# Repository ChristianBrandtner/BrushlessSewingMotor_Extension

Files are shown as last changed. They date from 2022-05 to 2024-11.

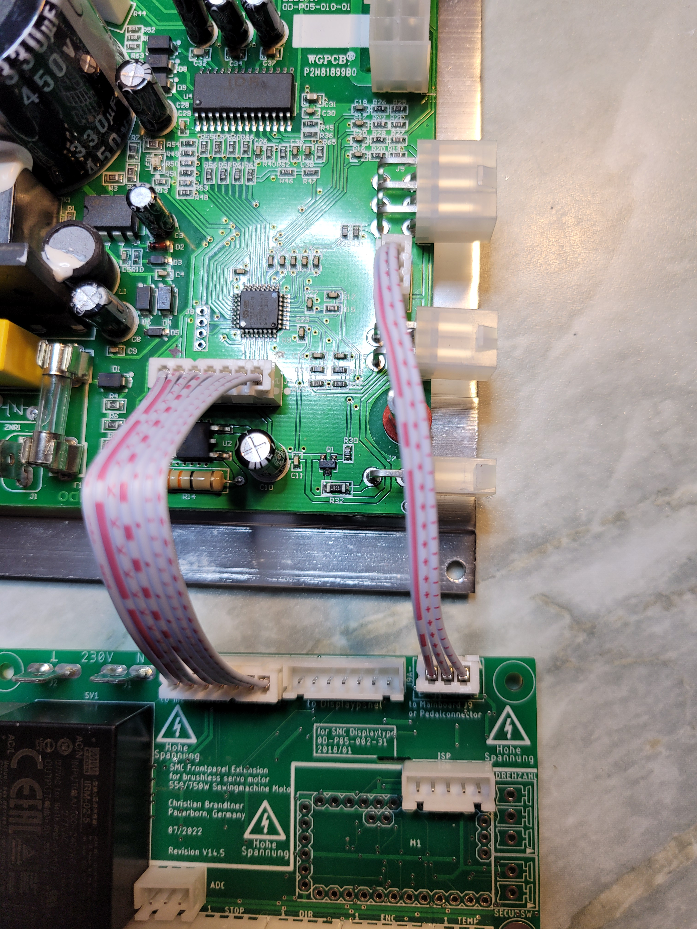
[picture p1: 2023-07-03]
Hardware/WithGalvanicIsolation/Arduino/picture/20221205_171128.jpg

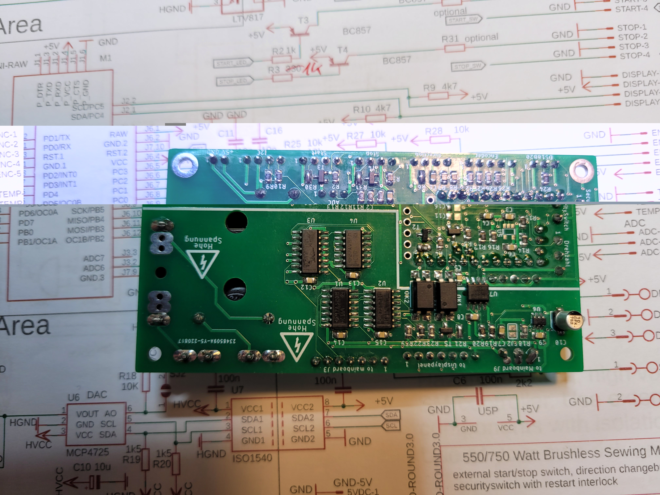
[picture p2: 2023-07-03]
Hardware/WithGalvanicIsolation/Arduino/picture/20221206_175256.jpg

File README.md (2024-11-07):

# BrushlessSewingMotor_Extension
&nbsp;&nbsp;&nbsp;&nbsp;&nbsp;&nbsp;&nbsp;&nbsp;&nbsp;&nbsp;


contact: github1@brandtner.net

## 11/2022  ! Project is in progress, ask before you order PCB or other things. !

## INTRODUCTION

This is a extension for a cheap chinese 550/750W brushless servo motor for external control of speed, direction, etc.
to use in in e.g. Mini Lathe

first test with switch and potentiometer:
https://www.youtube.com/watch?v=qao7Rex1lZU

SMC_Motor

## STATUS
7.11.2024

Ein neues ISO Interface ist in Arbeit aber noch nicht fertiggestellt. 
Die Software ermöglicht es jetzt die komplette Steuerung des Motorkontollers zu übernehmen, inklusive der Einstellungen für die Motorparameter im Kontroller. Das bedeutet daß das Bedienpanel des BLDC-Motors nicht mehr in Griffweite sein muss.

Im Moment pausiert die Entwicklung weil zuwenig Bedarf dafür zu erkennen ist.

A new ISO interface is in the works but not yet finished. The software now makes it possible to take over complete control of the motor controller, including the settings for the motor parameters in the controller. This means that the control panel of the BLDC motor no longer has to be within reach.

Development is currently on hold because there is not enough demand for it.

14.2.2023



RPM Sensor



05.09.2022

Beim Einbau in das Steuergehäuse habe ich nun festgestellt das es Änderungsbedarf gibt, es ist ziemlich eng und die Anordnung der Anschlüsse passt nicht so wirklich gut.
Eingebaut_V1

Deshalb wird es eine zweigeteilte Lösung geben, 1. das Iso Ínterface, montiert auf dem SMC Controller, 2. davon getrennt die Steuerungsplatine, dann neu mit einem Ardunino Nano wegen der USB-Schnittstelle für einfache Updates.
Durch die Trennung ergibt sich auch die Mögichkeit eine andere Steuerung zu verwenden, z.B. Blackpill STM32F411. Der Ardunio ist schon arg an der Grenze des Flashspeichers.
Steuerung_geplant

Next Version (11/2022):

IsoInterface_geplant_v16

08.07.2022

Die ursprüngĺiche Planung auf eine Hardwaredrehzahlmessung zu verzichten werde ich nicht mehr weiterverfolgen.
Die Softwarelösung funktioniert zwar zufriedenstellend, auch unter berücksichtigung des Getriebeschalters und der Untersetzungen von Motor und Getriebe, aber der Atmega ist durch die vielen Einstellungsmenüs am Ende der Kapazität.
Deshalb ist ein Drehzahlsensor an der Spindel erforderlich, damit entfällt die ganze Software für die Drehzahlberechnung und es ist Platz um die Schnittgeschwindigkeit für den Werkstückdurchmesser anzuzeigen.
Das finde ich nützlicher als den Drehzahlsensor einzusparen.
An der Hardware der Platine ändert sich nichts, war alles schon vorgesehen.

07.07.2022

Version 14.5

Änderungen an der Platine
Grund:
Einfügen eines optionalen ISP-Steckers.
Anschluss der RPM Sensors nach PB0 (ICP1) verlegt.
optinonal weitere Anschlussbuchse für den Pedalanschluss vorgesehen, zum direkten Kabelanschluss des Pedalkabels
an den originalen Stecker des SMC. Kein zusätzlicher JST Stecker J9 auf dem SMC Board notwendig. 

22.6.2022

Version 14.2

Änderungen an der Platine
Grund:
JST Stecker J3 Fehler in der Ausrichtung beseitigt

20.6.2022

Version 14.1

Änderungen an der Platine
Grund:
OK2 Anschlüsse vertauscht, optionale Widerstände R6,R30,R31
JST Stecker J3, Ausrichtung getauscht damit fertig konfektionierte Kabel zum SMC verwendet werden können.
Schaltung getestet (ohne RPM-Sensor und analog 0-10V Eingang, alles optional)

Wesentliche Funktionen der Software funktionieren:
Drehzahlregelung, Richtungsumschaltung, Drehzahlanzeige

03.06.2022 New PCB Version 12.2, Errors in PCB layout fixed. Basic software in progress.

12.05.2022 PCB Version 11.5 with galvanic isolation is in production 

30.04.2022 The goal is to fit the SMC controller board and everything else into the existing lathe front casing.

29.04.2022 optoisolation with separate powersupply is in work.

28.04.2022 under construction and brainstorming.

## PREVIEW

Display3
Display4

## TODO

TODO: finalize software

## Features

- no changes on Controlerboard or Panelboard needed; 
- can be installed in the housing on existing attachments; 
- speedcontrol, rotary encoder;
- start/stop control,  button with LED; 
- rotation direction control, button with LED;
- securityswitch input for chuck guard;
- spindel RPM display (calculated and maesured)
- original SMC displaypanel can be used at same time 
- high temperture warning;
- rampup and down at start/stop
- isolated inputs/outputs for galvanic isolation from the mains voltage

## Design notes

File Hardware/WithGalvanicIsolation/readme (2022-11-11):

11.11.2022
Version 14.5 only for testing, not production.

The next version consists of two boards, ISO board and STM32 control board

07.07.2022
Version 14.5
Änderungen an der Platine
Grund:
Einfügen eines optionalen ISP-Steckers.
Anschluss der RPM Sensors nach PB0 (ICP1) verlegt.
optinonal weitere Anschlussbuchse für den Pedalanschluss vorgesehen, zum direkten Kabelanschluss des Pedalkabels
an den originalen Stecker des SMC. Kein zusätzlicher JST Stecker J9 auf dem SMC Board notwendig. 

22.6.2022
Version 14.2
Änderungen an der Platine
Grund:
JST Stecker J3 Fehler in der Ausrichtung beseitigt

20.6.2022
Version 14.1
Änderungen an der Platine
Grund:
OK2 Anschlüsse vertauscht, optionale Widerstände R6,R30,R31
JST Stecker J3, Ausrichtung getauscht damit fertig konfektionierte Kabel zum SMC verwendet werden können.
Schaltung getestet (ohne RPM-Sensor und analog 0-10V Eingang, alles optional)

3.6.2022
Version 12.2
Änderungen an der Platine
Grund:
Fehler im Footprint des Arduino Pro Mini, J3.1 und J3.3 vertauscht
Signal Direction_SW von ADC7(A7) zu PB3(D11) verlegt ( wg. Arduino Kompatibilität)
Autorouter Layout verbessert

31.5.2022
Änderungen an der Platine
Neue Version 12.1
Grund:
SDA/SCL zwischen U6 und U7 vertauscht
C11 entfällt
C8,C5 näher an U7 Pins
R29 hinzu, für Betrieb ohne Displaypanel
R25,R26,R27,R28,C11,C26 Entprellung für Encoder hinzugefügt
Footprint für alternativen Sicherungshalter hinzugefügt
einige falsche Beschriftungen korrigiert
Kosmetik

30.5.2022
Platine 11.5 bestückt

12.5.2022
Platine V11.5 in Produktion

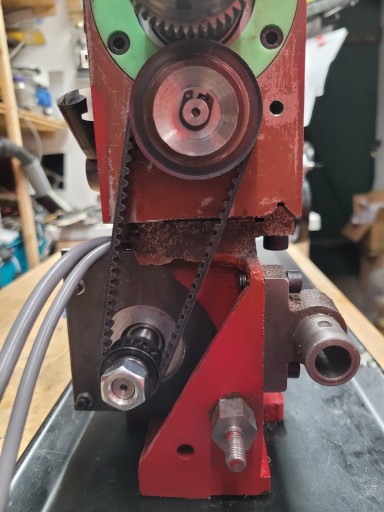
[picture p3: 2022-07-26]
Hardware/Lathe_EDM300/Motor3.jpg

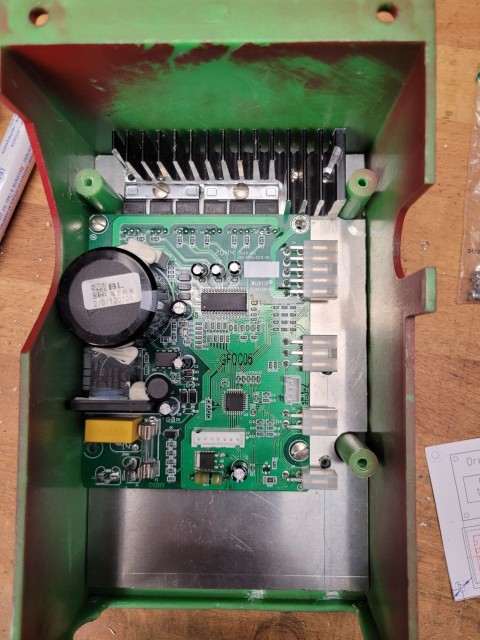
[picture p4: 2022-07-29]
Hardware/Lathe_EDM300/GrundPlatteImGehäuse.jpg

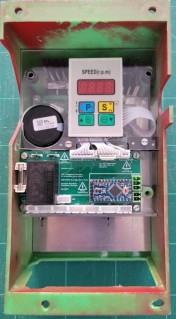
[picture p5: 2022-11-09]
Hardware/Lathe_EDM300/Eingebaut_V1.jpg

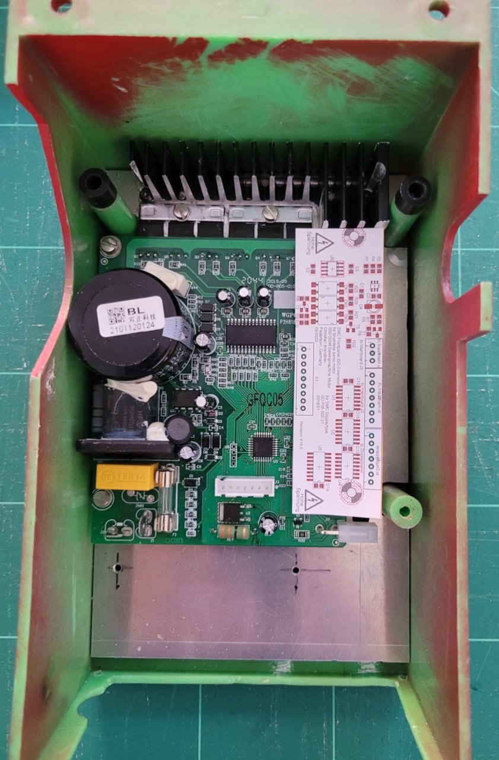
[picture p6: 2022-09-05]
Hardware/Lathe_EDM300/IsoInterface_geplant_v16.jpg

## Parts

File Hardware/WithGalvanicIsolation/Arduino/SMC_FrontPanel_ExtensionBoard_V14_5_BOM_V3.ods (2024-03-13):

Part | Value | Device | Package | Description | Link
5VDC | GND-5V -Connector | JST-XH-02-PIN-ROUND-PAD | JST-XH-02-PACKAGE-ROUND-PAD | JST XH Connector 2 Pin
ADC | ADC-Connector | JST-XH-03-PIN-ROUND-PAD | JST-XH-03-PACKAGE-ROUND-PAD | JST XH Connector 2 Pin
C1 | 100n | C-EUC0805 | C0805 | CAPACITOR, European symbol
C2 | 100n | C-EUC0805 | C0805 | CAPACITOR, European symbol
C3 | 1n | C-EUC0805 | C0805 | CAPACITOR, European symbol
C4 | 100n | C-EUC0805 | C0805 | CAPACITOR, European symbol
C5 | 100n | C-EUC0805 | C0805 | CAPACITOR, European symbol
C6 | 100n | C-EUC0805 | C0805 | CAPACITOR, European symbol
C7 | 100n | C-EUC0805 | C0805 | CAPACITOR, European symbol
C8 | 100n | C-EUC0805 | C0805 | CAPACITOR, European symbol
C9 | 100n | C-EUC0805 | C0805 | CAPACITOR, European symbol
C10 | 10u | CPOL-EU153CLV-0405 | 153CLV-0405 | POLARIZED CAPACITOR, European symbol
C11 | 10n | C-EUC0805 | C0805 | CAPACITOR, European symbol
C12 | 100n | C-EUC0805 | C0805 | CAPACITOR, European symbol
C13 | 100n | C-EUC0805 | C0805 | CAPACITOR, European symbol
C14 | 100n | C-EUC0805 | C0805 | CAPACITOR, European symbol
C15 | 100n | C-EUC0805 | C0805 | CAPACITOR, European symbol
C16 | 10n | C-EUC0805 | C0805 | CAPACITOR, European symbol
DIR | Direction-Connector | JST-XH-04-PIN-ROUND-PAD | JST-XH-04-PACKAGE-ROUND-PAD | JST XH Connector 2 Pin
DISPLAY | I2C-Connector | JST-XH-04-PIN-ROUND-PAD | JST-XH-04-PACKAGE-ROUND-PAD | JST XH Connector 2 Pin
DREHZAHL | Connector | MCV_1.5/3/-G-3.5 | 1843619
ENC | ENCODER-Connector | JST-XH-05-PIN-ROUND-PAD | JST-XH-05-PACKAGE-ROUND-PAD | JST XH Connector 2 Pin
F1 | 0,05A (0,1A) | FUSE 0,05A | MTA501100 | Fuse
F2 |  | SHK20L | SHK20L | FUSE HOLDER 5 x 20 mm, SH contact, SHH1 Schukat, E1073 Buerklin
ISP | ISP-Connector | JST-XH-05-PIN-ROUND-PAD | JST-XH-05-PACKAGE-ROUND-PAD | JST XH Connector 2 Pin
J1 | !!Do not equip J1 on SMC PCB!! | Important!! | Solder JST Connector direct on Arduino Mini Pro
J2 | PIN2F061.060 | PIN2F061.060 | F061.060 | Flachstecker Typ Tyco/Electronics/AMP TAB, FASTON
J3 | to mainboardconnector J3 Connector | JST-XH-07-PIN-ROUND-PAD | JST-XH-07-PACKAGE-ROUND-PAD | JST XH Connector 2 Pin
J4 | to Displaypanel Connector | JST-XH-07-PIN-ROUND-PAD | JST-XH-07-PACKAGE-ROUND-PAD | JST XH Connector 2 Pin
J9 | Connector | JST-XH-03-PIN-ROUND-PAD | JST-XH-03-PACKAGE-ROUND-PAD | JST XH Connector 2 Pin
J9A- | Alternative Connector | MCV_1.5/3/-G-3.5 | 1843619
M1 | ARDUINO-PRO-MINI-RAW | ARDUINO-PRO-MINI-RAW | ARDUINO-PRO-MINI
OK1 | LTV817 |  | SMD4-7 | Optocoupler, Phototransistor Output, Low Input Current
OK2 | LTV817 |  | SMD4-7 | Optocoupler, Phototransistor Output, Low Input Current
R1 | 330 | R-EU_R0805 | R0805 | RESISTOR, European symbol
R2 | 1k | R-EU_R0805 | R0805 | RESISTOR, European symbol
R3 | 330 | R-EU_R0805 | R0805 | RESISTOR, European symbol
R4 | 1k | R-EU_R0805 | R0805 | RESISTOR, European symbol
R5 | 1k | R-EU_R0805 | R0805 | RESISTOR, European symbol
R6 | optional | R-EU_R0805 | R0805 | RESISTOR, European symbol
R7 | 2k2 | R-EU_R0805 | R0805 | RESISTOR, European symbol
R8 | 1k | R-EU_R0805 | R0805 | RESISTOR, European symbol
R9 | 4k7 | R-EU_R0805 | R0805 | RESISTOR, European symbol
R10 | 4k7 | R-EU_R0805 | R0805 | RESISTOR, European symbol
R11 | 220 | R-EU_R0805 | R0805 | RESISTOR, European symbol
R12 | 15k | R-EU_R0805 | R0805 | RESISTOR, European symbol
R13 | 15k | R-EU_R0805 | R0805 | RESISTOR, European symbol
R14 | 1k | R-EU_R0805 | R0805 | RESISTOR, European symbol
R15 | 2k2 | R-EU_R0805 | R0805 | RESISTOR, European symbol
R16 | 1k | R-EU_R0805 | R0805 | RESISTOR, European symbol
R17 | 2k2 | R-EU_R0805 | R0805 | RESISTOR, European symbol
R18 | 10K | R-EU_R0805 | R0805 | RESISTOR, European symbol
R19 | 1k5 | R-EU_R0805 | R0805 | RESISTOR, European symbol
R20 | 1k5 | R-EU_R0805 | R0805 | RESISTOR, European symbol
R21 | 0 | R-EU_R0805 | R0805 | RESISTOR, European symbol
R22 | 1K | R-EU_R0805 | R0805 | RESISTOR, European symbol
R23 | 10K | R-EU_R0805 | R0805 | RESISTOR, European symbol
R24 | 4k7 | R-EU_R0805 | R0805 | RESISTOR, European symbol
R25 | 10k | R-EU_R0805 | R0805 | RESISTOR, European symbol
R26 | 10k | R-EU_R0805 | R0805 | RESISTOR, European symbol
R27 | 10k | Do not equip if the encoder used has a circuit board with resistors |  | RESISTOR, European symbol
R28 | 10k | Do not equip if the encoder used has a circuit board with resistors |  | RESISTOR, European symbol
R29 | 10K | R-EU_R0805 | R0805 | RESISTOR, European symbol
R30 | optional | R-EU_R0805 | R0805 | RESISTOR, European symbol
R31 | optional | R-EU_R0805 | R0805 | RESISTOR, European symbol
SECURSW | Connector | MCV_1,5/2-G-3,5 | 1843606
START | Start-Connector | JST-XH-04-PIN-ROUND-PAD | JST-XH-04-PACKAGE-ROUND-PAD | JST XH Connector 2 Pin
STOP | STOP-Connector | JST-XH-04-PIN-ROUND-PAD | JST-XH-04-PACKAGE-ROUND-PAD | JST XH Connector 2 Pin
SV1 | IRM-02-5 | IRM-02-X | IRM-02-X | Murata AC-DC Converter 230V AC to 5V DC
T1 | BC857 | BC857C-PNP-SOT23-BEC | SOT23-BEC | PNP Transistror
T2 | BC857 | BC857C-PNP-SOT23-BEC | SOT23-BEC | PNP Transistror
T3 | BC857 | BC857C-PNP-SOT23-BEC | SOT23-BEC | PNP Transistror
T4 | BC857 | BC857C-PNP-SOT23-BEC | SOT23-BEC | PNP Transistror
T5 | BC857 | BC857C-PNP-SOT23-BEC | SOT23-BEC | PNP Transistror
TEMP | DS18B20-Connector | JST-XH-03-PIN-ROUND-PAD | JST-XH-03-PACKAGE-ROUND-PAD | JST XH Connector 2 Pin
U1 | 74HC164 | 74HC164D | SO14 | 8-bit parallel out SHIFT REGISTER
U2 | 74HC164 | 74HC164D | SO14 | 8-bit parallel out SHIFT REGISTER
U3 | 74HC165 | 74HC165D | SO16 | 8-bit parallel load SHIFT REGISTER
U4 | 74HC00 | 74HC00D | SO14 | Quad 2-input NAND gate
U5 | 74LVC1G17DBV | 74LVC1G17DBV | SOT23-5 | Single Schmitt-Trigger Buffer
U6 | MCP4725 | MCP4725SOT-23 | SOT23-6 | MCP4725 DAC | If not available, alternative: https://www.adafruit.com/product/935
U7 | ISO1540 | ISO1540 | SO-08 |  | If not available, alternative: https://www.adafruit.com/product/4903
1 | DS18B20 | one-wire temperature Sensor |  |  | https://de.aliexpress.com/item/4000895660165.html
 | Display | 0,96"Weiß OLED Modul I2C Interface 128x64 |  |  | https://de.aliexpress.com/item/4000895660165.html
or | Display | 1,3 "Weiß OLED Modul I2C Interface 128x64 |  |  | https://de.aliexpress.com/item/4000895660165.html
1 | RPM Sensor | NJK-5001C hall-sensor-schalter M8 DC5-3 |  |  | https://de.aliexpress.com/item/32750312763.html
1 | Rotary Encoder | Rotary Encoder Modul EC11 | Knob Cap EC11 |  | https://de.aliexpress.com/item/1005004406791966.html
3 | Button with LED 5V | Waterproof Metall Push Button | Momentary self-reset, China, 3-9V(5V), 16mm |  | https://de.aliexpress.com/item/4001291695467.html
1 | security stop button |  | 16mm, 1NO1NC, Without Harness |  | https://de.aliexpress.com/item/1005003048332754.html

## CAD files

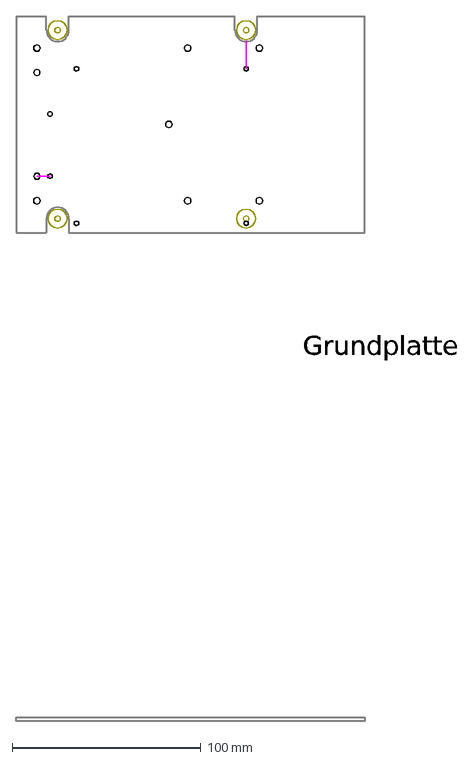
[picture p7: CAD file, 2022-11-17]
Hardware/Lathe_EDM300/Grundplatte_Steuerung.dxf
Grundplatte

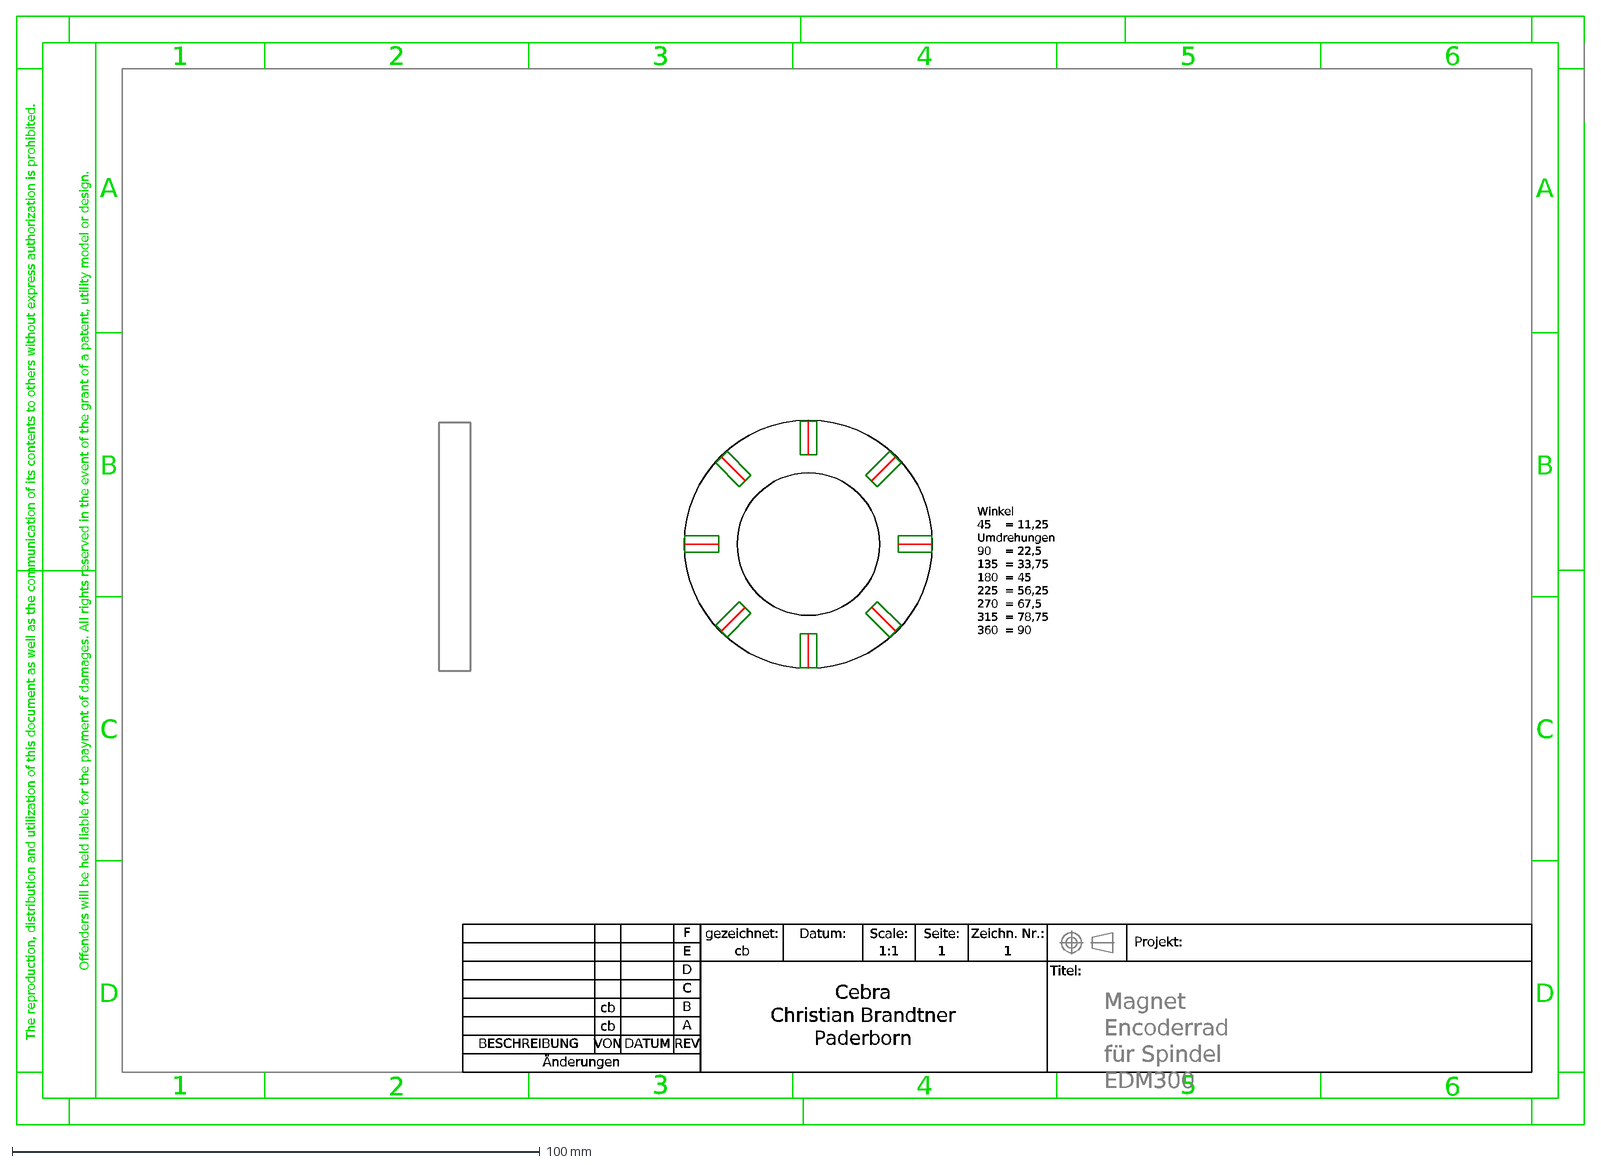
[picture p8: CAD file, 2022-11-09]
Hardware/Lathe_EDM300/MagnetEncoderRad.dxf
6
5
1
2
3
4
A
B
C
D
The reproduction, distribution and utilization of this document as well as the communication of its contents to others without express authorization is prohibit
Offenders will be held liable for the payment of damages. All rights reserved in the event of the grant of a patent, utility model or design.
1:1
cb
Zeichn. Nr.:
gezeichnet:
Datum:
Scale:
Seite:
Projekt:
Titel:
Cebra Christian Brandtner Paderborn
E
F
Änderungen
BESCHREIBUNG
VON
DATUM
REV
Winkel 45 = 11,25 Umdrehungen 90 = 22,5 135 = 33,75 180 = 45 225 = 56,25 270 = 67,5 315 = 78,75 360 = 90
Magnet Encoderrad für Spindel EDM300

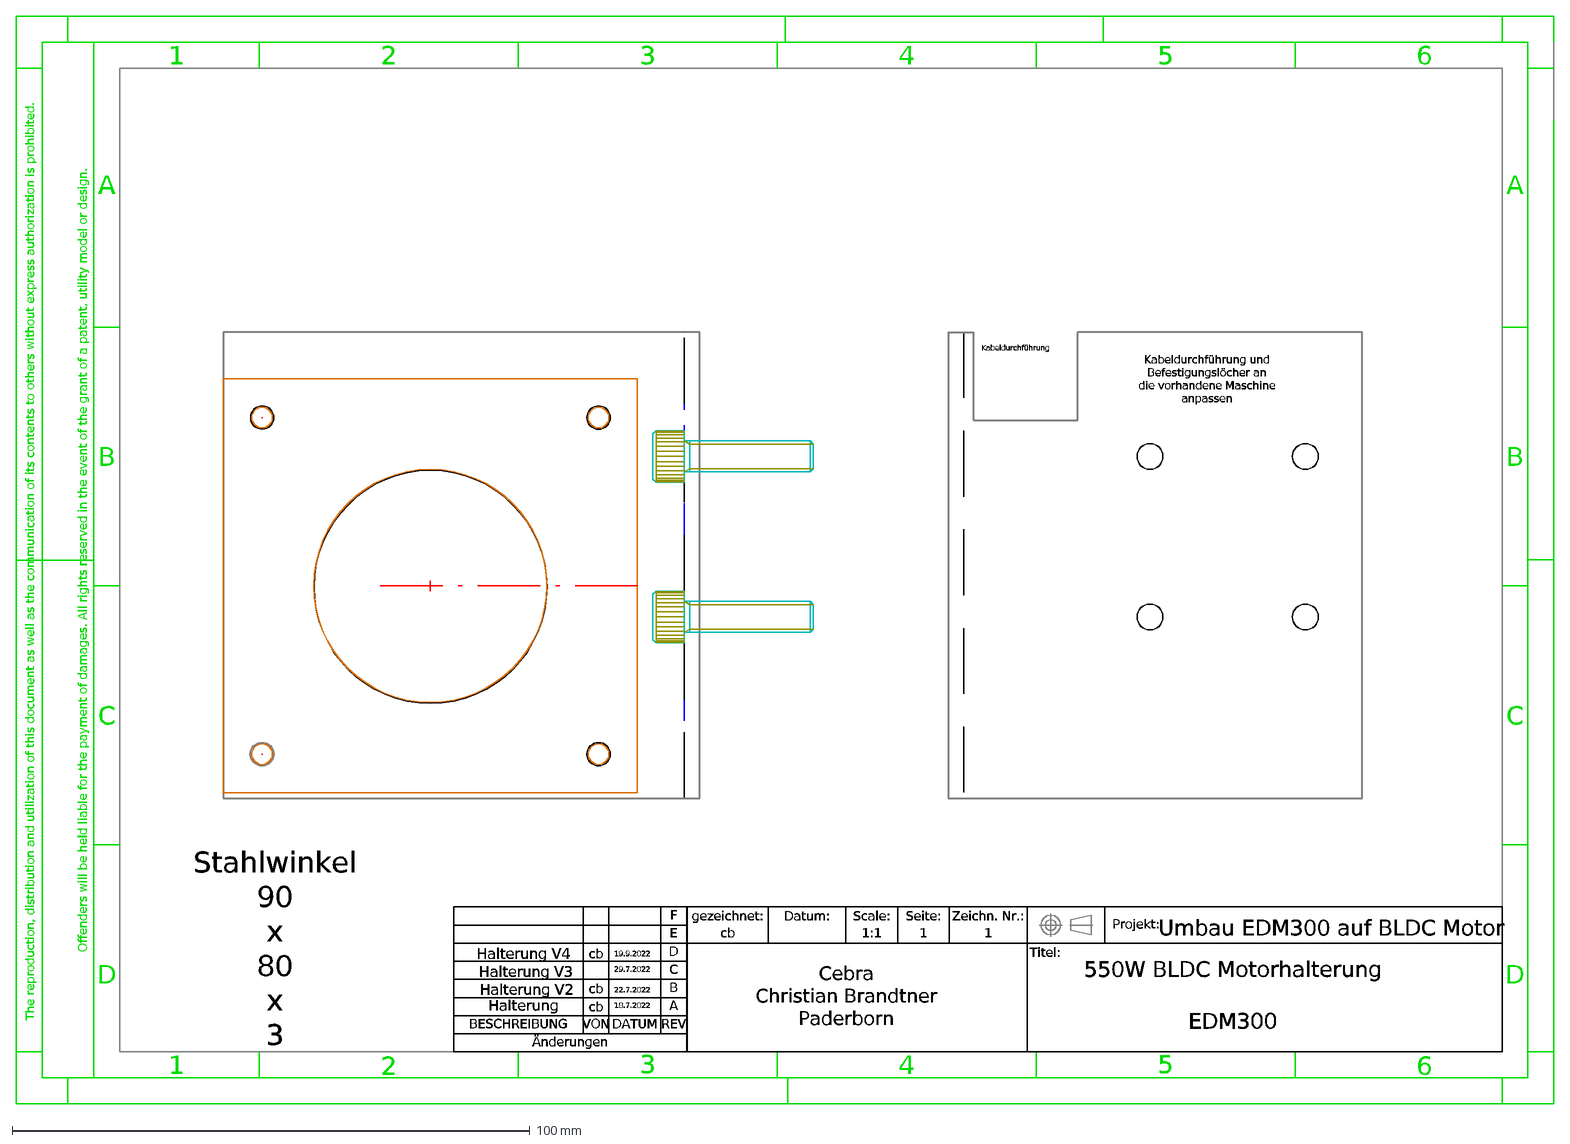
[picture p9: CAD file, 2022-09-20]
Hardware/Lathe_EDM300/Motorhalterung4.dxf
6
5
1
2
3
4
A
B
C
D
The reproduction, distribution and utilization of this document as well as the communication of its contents to others without express authorization is prohibit
Offenders will be held liable for the payment of damages. All rights reserved in the event of the grant of a patent, utility model or design.
1:1
cb
Zeichn. Nr.:
gezeichnet:
Datum:
Scale:
Seite:
Projekt:
Titel:
Cebra Christian Brandtner Paderborn
E
F
Änderungen
BESCHREIBUNG
VON
DATUM
REV
550W BLDC Motorhalterung EDM300
Umbau EDM300 auf BLDC Motor
18.7.2022
22.7.2022
29.7.2022
19.9.2022
Kabeldurchführung
Kabeldurchführung und Befestigungslöcher an die vorhandene Maschine anpassen
Halterung
Halterung V2
Halterung V3
Halterung V4
Stahlwinkel 90 x 80 x 3

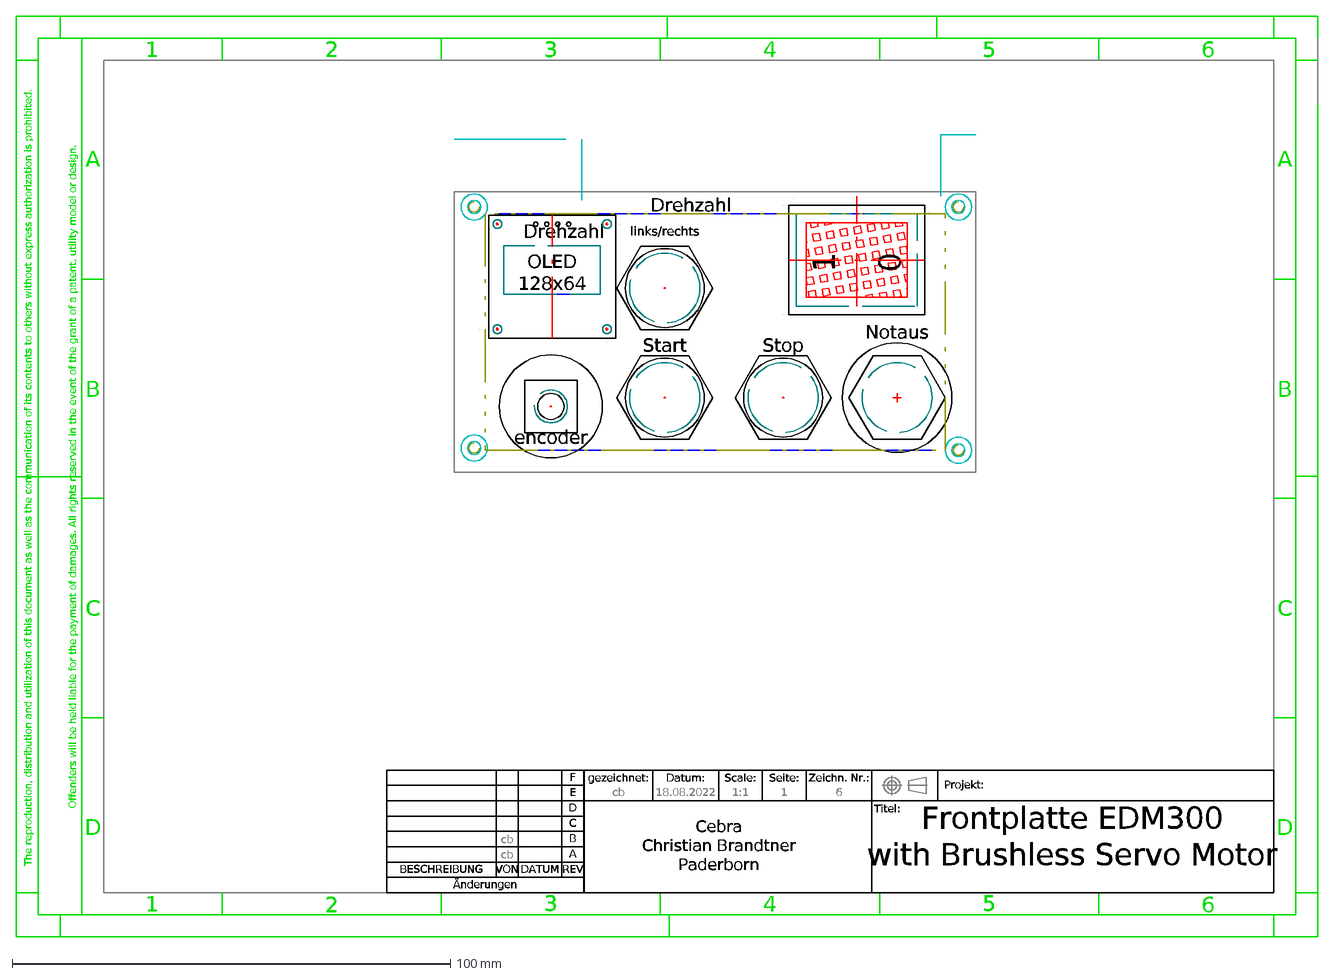
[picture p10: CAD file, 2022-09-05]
Hardware/Lathe_EDM300/Frontplatte_V5.dxf
6
5
1
2
3
4
A
B
C
D
The reproduction, distribution and utilization of this document as well as the communication of its contents to others without express authorization is prohibit
Offenders will be held liable for the payment of damages. All rights reserved in the event of the grant of a patent, utility model or design.
1:1
18.08.2022
cb
Zeichn. Nr.:
gezeichnet:
Datum:
Scale:
Seite:
Projekt:
Titel:
Cebra Christian Brandtner Paderborn
E
F
Änderungen
BESCHREIBUNG
VON
DATUM
REV
Frontplatte EDM300 with Brushless Servo Motor
0
encoder
links/rechts
Start
Stop
Notaus
Drehzahl
OLED 128x64

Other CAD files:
Hardware/Lathe_EDM300/Drehzahlsensor_Halterung.dxf

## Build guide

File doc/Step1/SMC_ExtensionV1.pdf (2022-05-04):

# BRUSHLESS SERVO MOTOR Panelextension

# Overview SMC (Sewing Motor Controler)

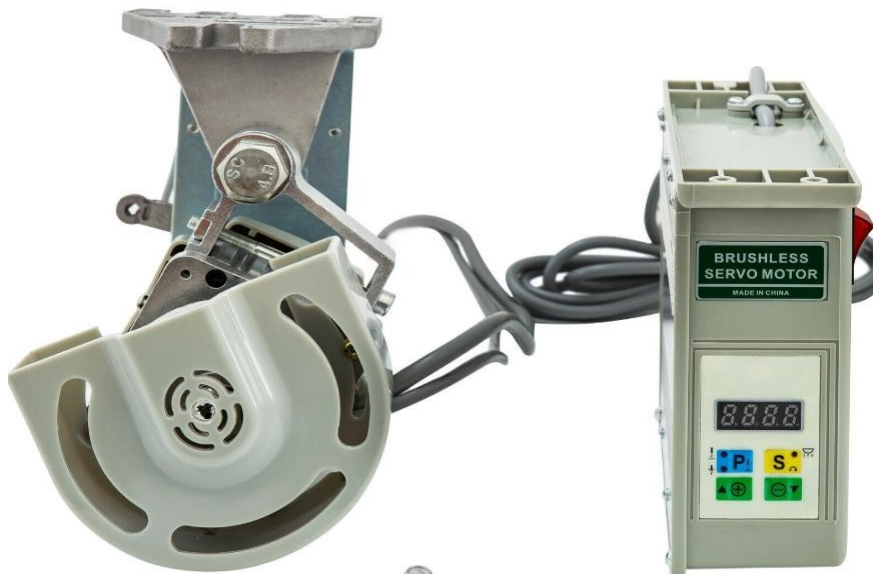
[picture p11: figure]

https://de.aliexpress.com/item/1005003090904992.html?spm=a2g0o.store_pc_allProduct.8148356.1.15fa6fc5JvWeOf

search: „brushless servo motor 550W“ at Aliexpress or Ebay

Extension for cheap chinese brushless sewingmachine motor to control speed, start/stop, direction, etc.

This Servomotor is available with 550W or 750W and could be used as a replacement for the motor in mini lathe like Rotwerk EDM300 and similar machines.

# 4 no changes on Controlerboard or Panelboard needed 4 can be installed in the housing on existing attachments 4 speedcontrol, potentiometer 4 start/stop control, switch 4 rotation direction control, button with LED 4 securityswitch input for chuck guard 4 automatic reset thermostat input

# Features of SMC extension board

# Mainboard and Panelboard

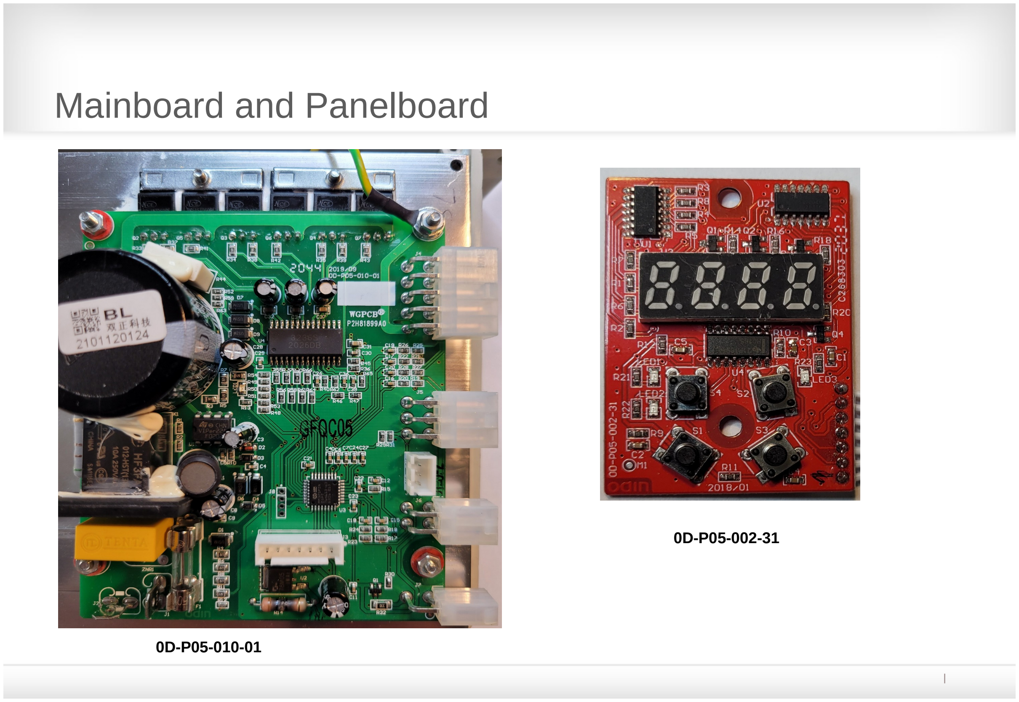
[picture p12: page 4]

0D-P05-010-01

0D-P05-002-31

# SMC Extension between main and panel

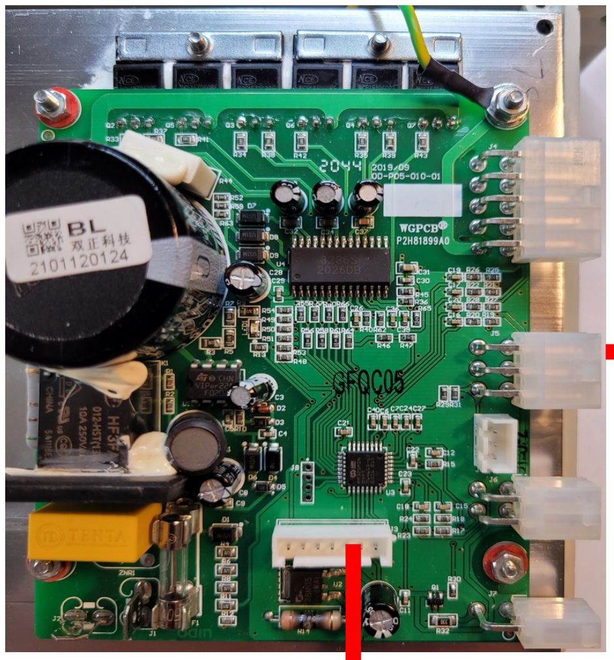
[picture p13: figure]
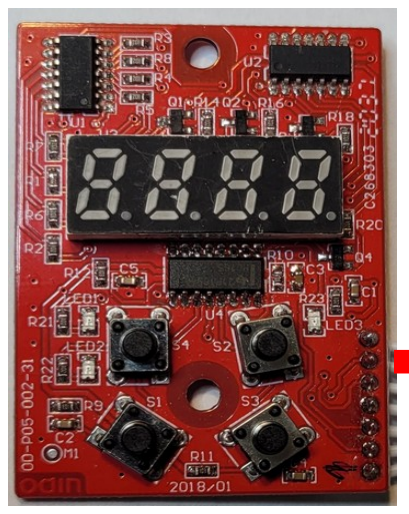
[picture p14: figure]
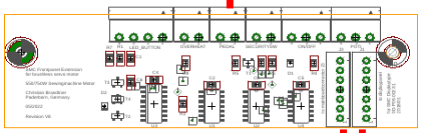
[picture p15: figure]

# SMC Extension external connection

Direction switch with Led | Overheat switch (optional)

Chuck guard
switch

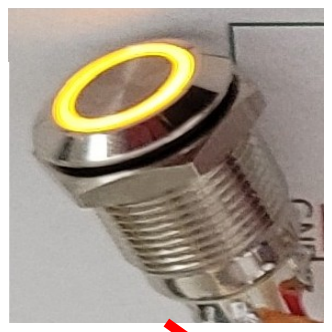
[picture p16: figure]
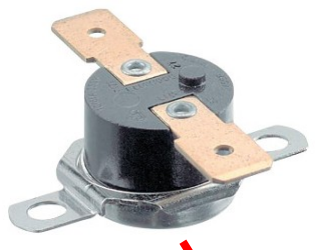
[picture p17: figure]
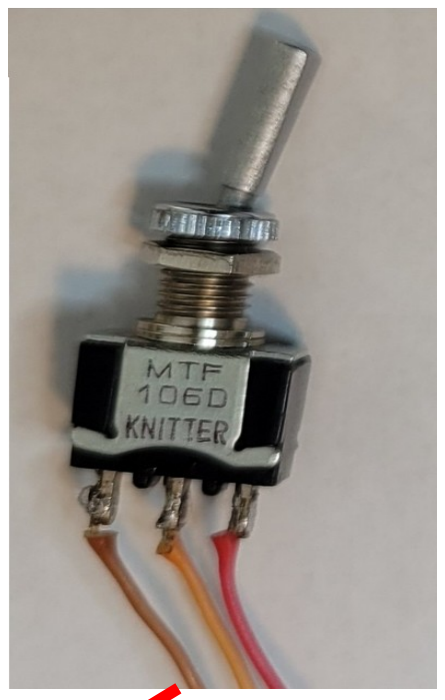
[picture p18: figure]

On/off
switch

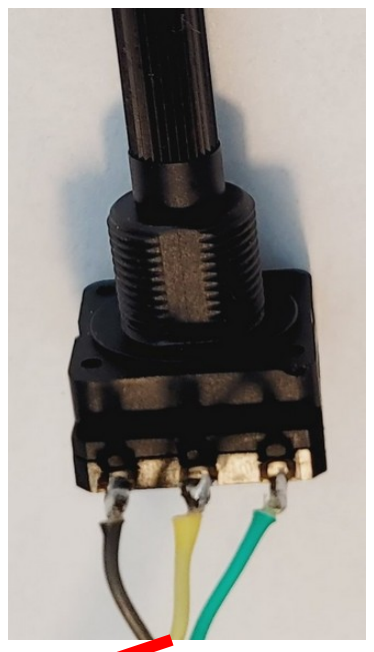
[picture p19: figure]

Speed
Potentiometer

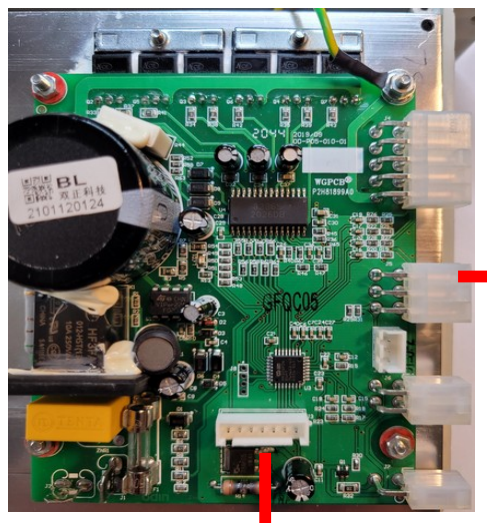
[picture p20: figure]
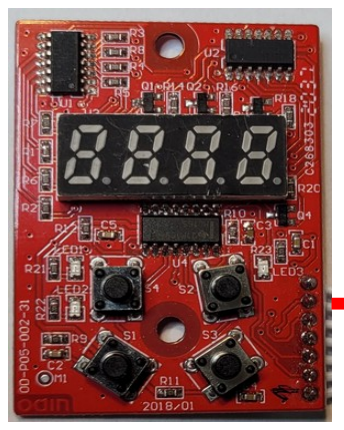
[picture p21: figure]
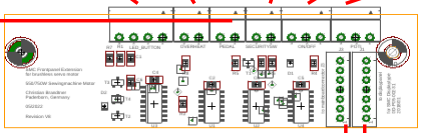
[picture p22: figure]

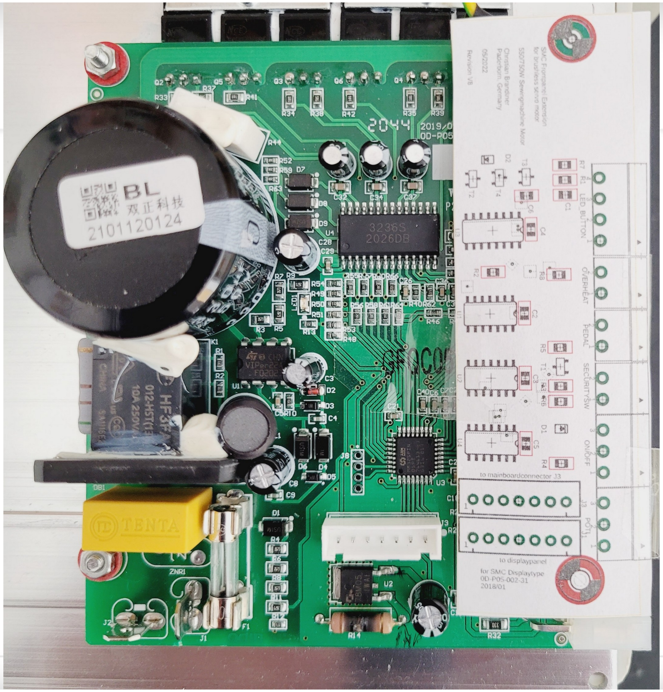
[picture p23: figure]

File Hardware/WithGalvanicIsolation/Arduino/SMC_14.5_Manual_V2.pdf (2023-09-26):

# SMC-Extension PCB 14.5

Extension of an inexpensive sewing machine motor with an

additional control for easy switching on/off, changing the

direction of rotation and controlling the speed.

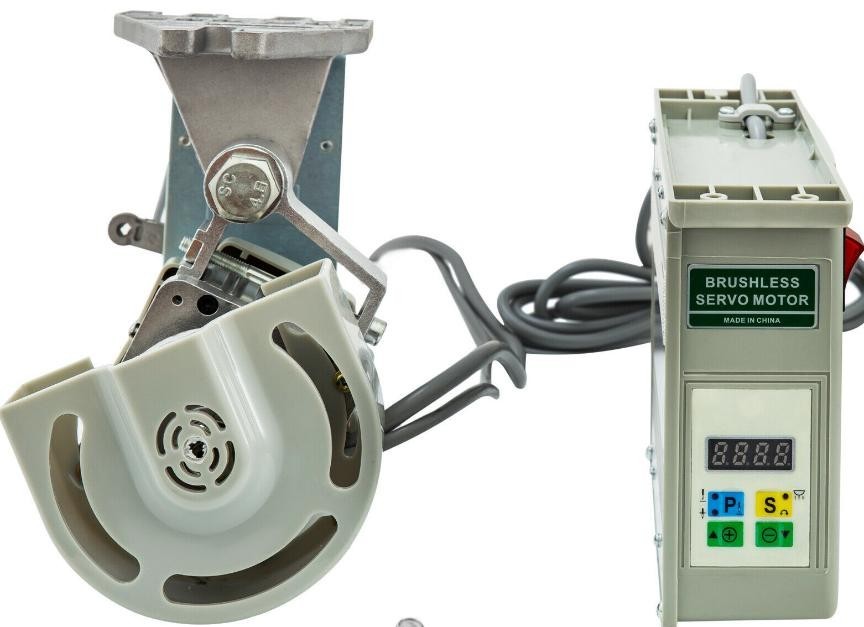
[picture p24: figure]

An EDM300 lathe is intended for installation in the control

housing.

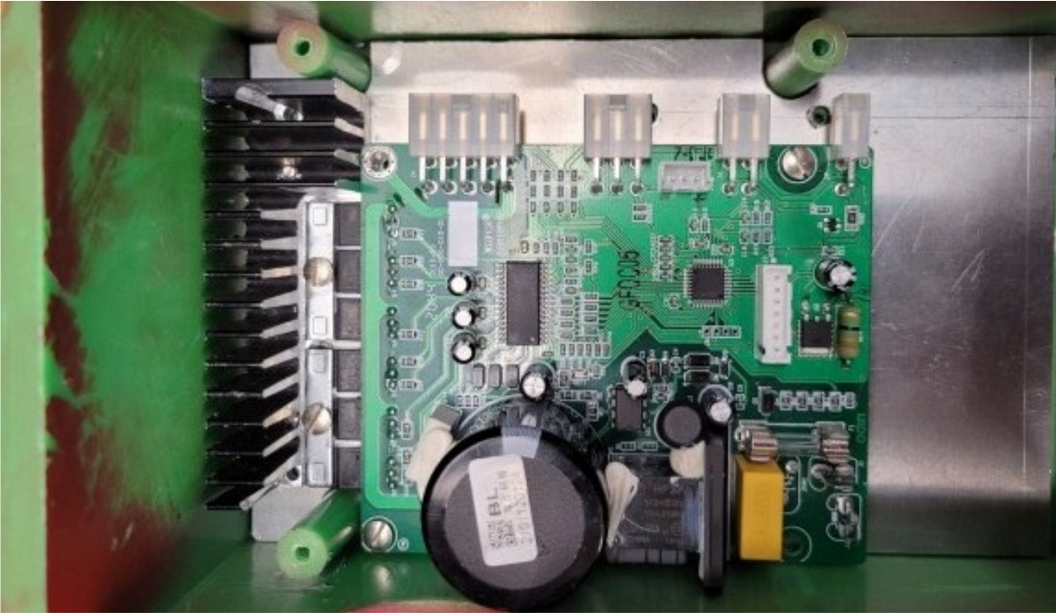
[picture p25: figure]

Sample front panel on the lathe

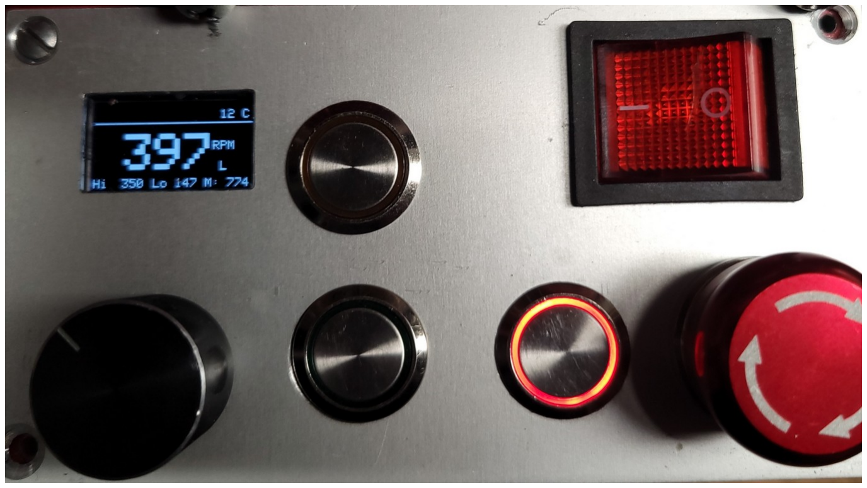
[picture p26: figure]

230V

# Netzspannung

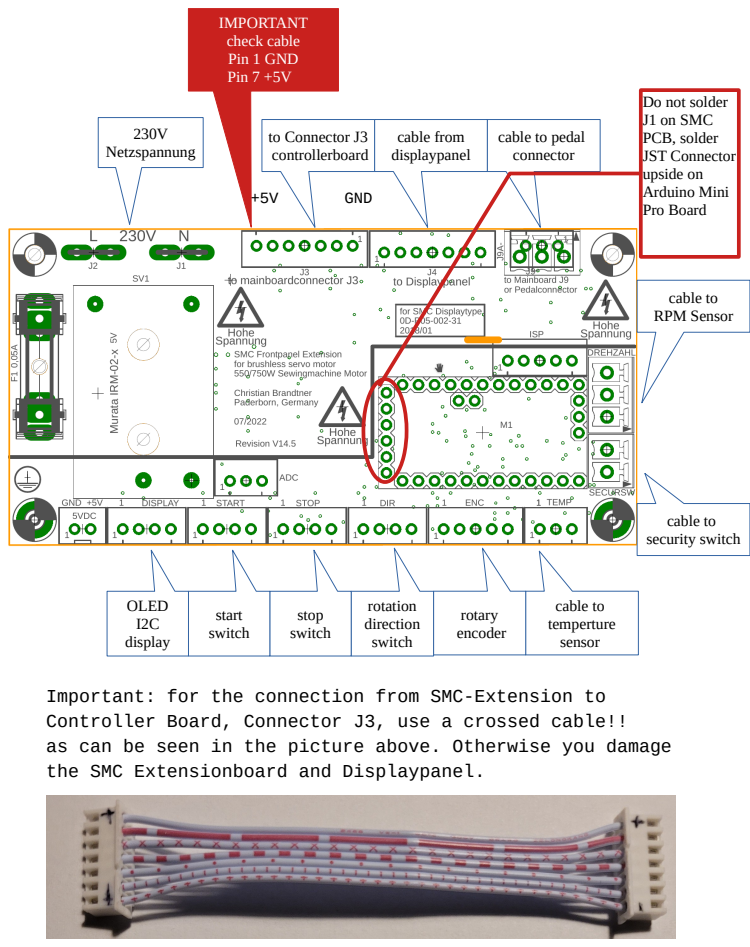
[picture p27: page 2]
GND; as can be seen in the picture above.; Otherwise you damage; to Connector J3 controllerboard; cable from displaypanel; cable to RPM Sensor; cable to security switch; cable to temperture sensor; rotary encoder; rotation direction switch; stop switch; start switch; OLED I2C display; IMPORTANT check cable Pin 1 GND Pin 7 +5V

Do not solder
J1 on SMC
PCB, solder
JST Connector
upside on
Arduino Mini
Pro Board

cable to pedal
connector

Important: for the connection from SMC-Extension to

Controller Board, Connector J3, use a crossed cable!!

the SMC Extensionboard and Displaypanel.

# plug assignment

Pedalcable connector J9

use original cable from controller

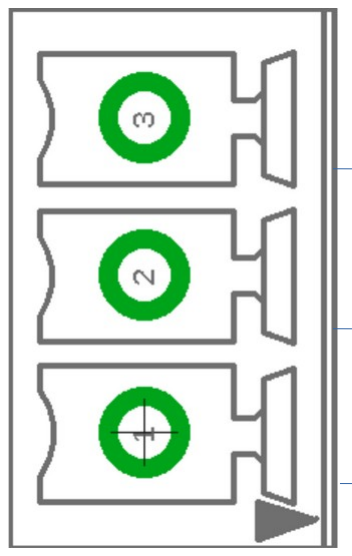
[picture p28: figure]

RPM sensor cable

use optical or hall effect sensor

e.g. NJK-5001C, hall effect sensor NPN, 8mm

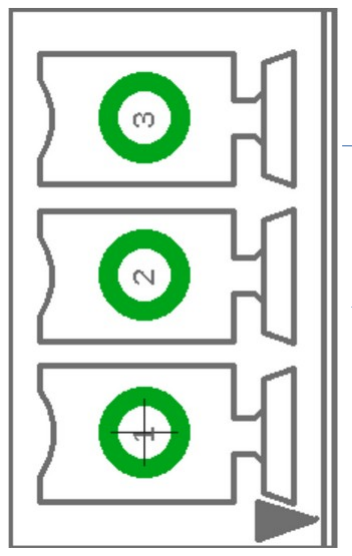
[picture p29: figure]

Drehzahl

Security switch

If motor is running and the security switch is opened, the motor

stops immediately (hard stop).

## SECURSW

# +5V, red

# GND, black

# Pedal, yellow

# load, black

# GND, blue

# +5V, brown

# GND

# security switch, NC = normaly closed

## Led + Switch Connector

use 5V Leds !

# 1 GND 2 LED 3 GND 4 Switch

## OLED Display

There are different displays on the market, the pin assignment +5V

and GND can be rotated, check it before power on.

# 1 GND

2 +5V

# 3 SCL 4 SDA

## Rotary Encoder

# 1 GND

2 A
3 B

# 4 Button

5 +5V

## Temperature sensor DS18B20

### 1 GND

2 onewire

3 +5V

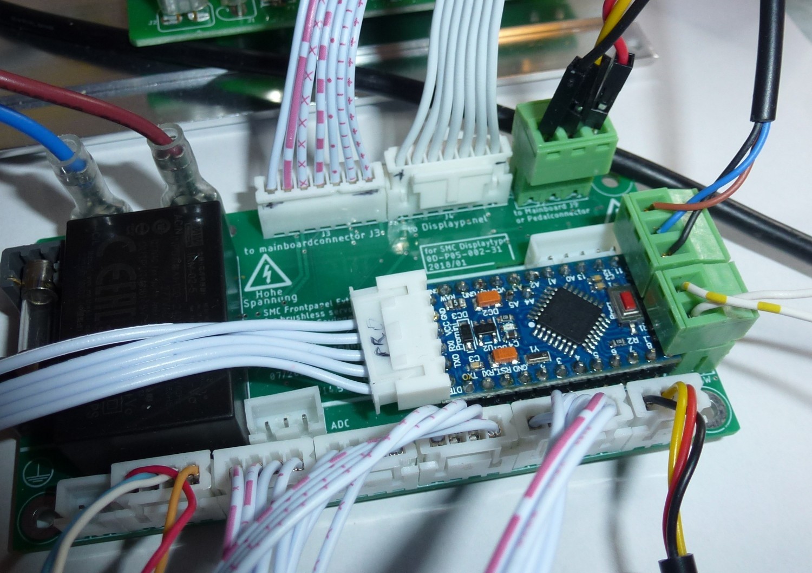
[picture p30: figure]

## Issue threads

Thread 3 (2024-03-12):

Reverse pin

jschoch, 2024-03-12:
I looked through your .ino source as well as the schematics.  The service manual has a pin called "inside up" mapped to pin 6 of the connector and you have some code for x1_6.  Is reversing the motor simply a matter of pulling this down?  I have a consew motor/driver and have been looking for an easy way to get it into reverse mode for a while...

ChristianBrandtner, 2024-03-13:
I don't know the meaning of pin 6. As far as I know, you can only reverse the direction of rotation using the S key or with my expansion board, where I simulate the S key to the controller board

jschoch, 2024-03-13:
can you clarify that you are just using the aruduino to "press" the buttons in a given sequence for the correct time periods, and that there is no pin available to just toggle the direction of the motor?

The consew motor also requies a "long press" and then navigate to the correct "parameter" and then to change it's value (0/1)

If the makers of these boards included a RS485 interface and some documentation I bet they'd sell a bunch more stuff...

ChristianBrandtner, 2024-03-13:
I only know the engine and controller that I use here. The controller communicates with the user panel via two serial connections. In principle SPI. Look in the circuit diagrams there is recognizable. Hardware shift registers for display and keys are used.
I cannot judge whether there is another way to control the controller. There is no internal information about the controller. I have determined the format of serial data with reverse engineering using a logic analyzer.

KingBain, 2025-01-02:
Have you seen what this creator has managed to do in terms of customizing these servo's and boards ?
https://www.youtube.com/watch?v=wpBil0FDSuQ

I wonder how theyre managing to do an direction control and emergency stop

ChristianBrandtner, 2025-01-03:
If you twisted two of the three engine connections and encoders twisted each other, the direction of rotation changes. You could do that with relays. This should not be done under supply voltage and can lead to high back EMF and to destroy the controller for BLDC engines. But I don't know how they did it. I have already thought about such a simple control

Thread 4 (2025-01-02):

Replacement mini lathe case

KingBain, 2025-01-02:
For others going down this path, I've created a 3d printable replacement case .
https://www.printables.com/model/1131449-mini-lathe-control-box

Its can be modified to be deeper... hold more electronics.

ChristianBrandtner, 2025-01-03:
Very nice idea

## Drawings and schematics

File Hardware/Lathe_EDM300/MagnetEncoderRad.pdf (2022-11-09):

1 | 2 | 3 | 4 | 5 | 6

A

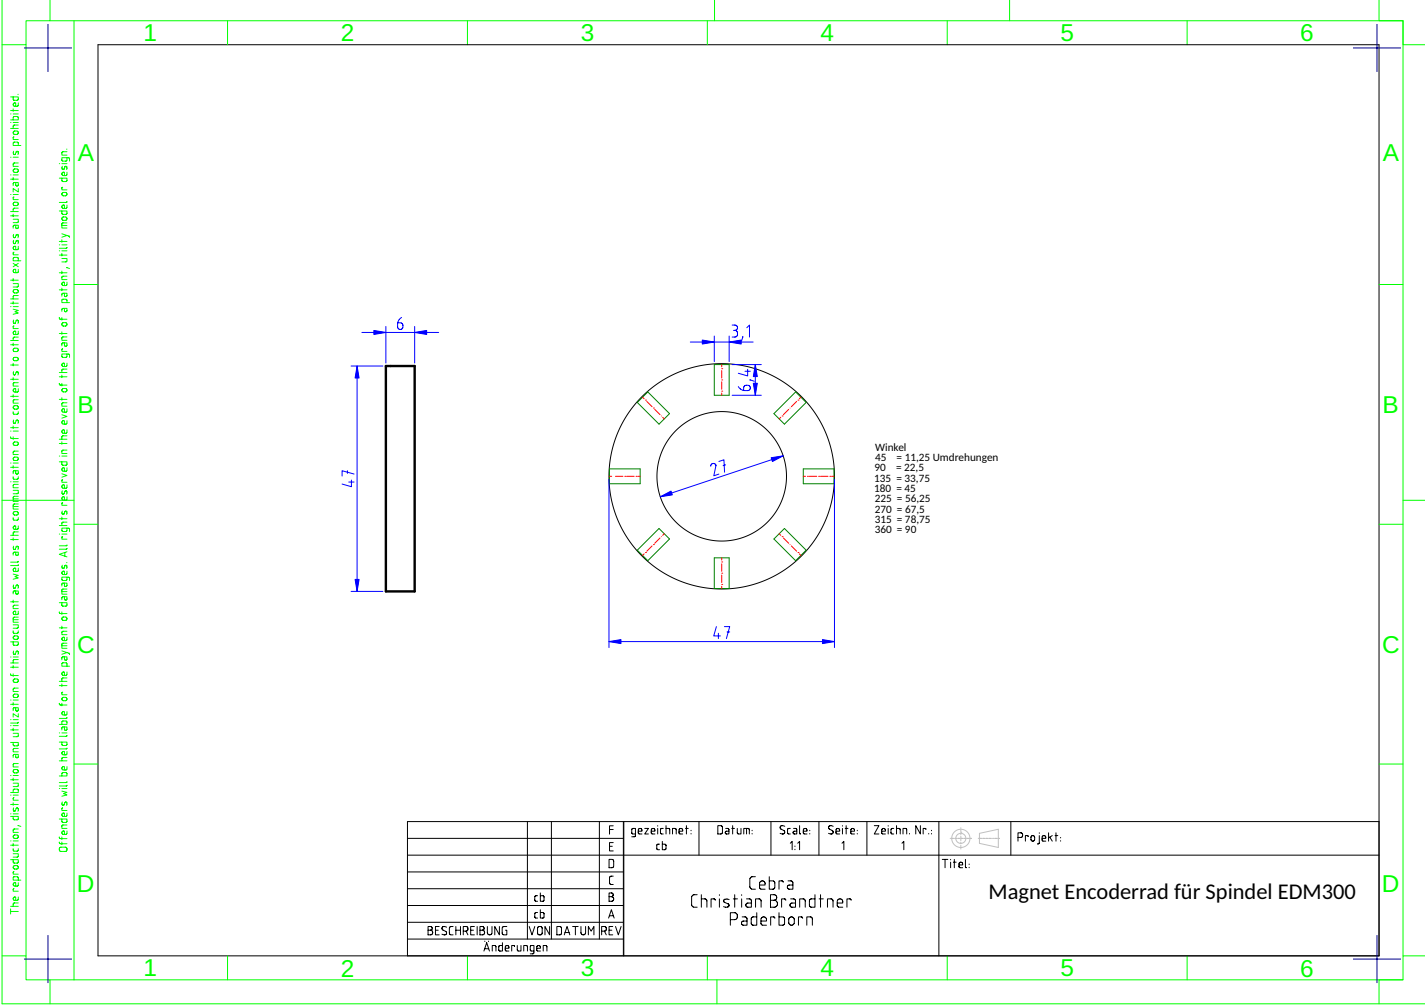
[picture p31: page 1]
Winkel 45 = 11,25 Umdrehungen

Magnet Encoderrad für Spindel EDM300

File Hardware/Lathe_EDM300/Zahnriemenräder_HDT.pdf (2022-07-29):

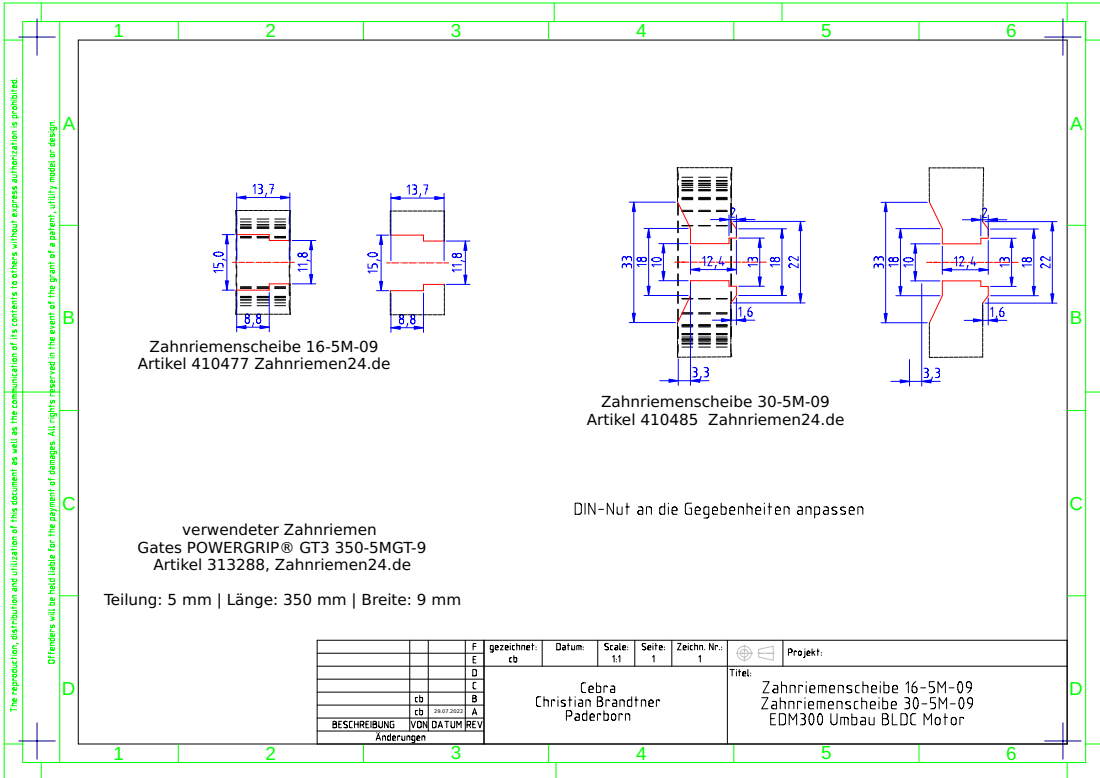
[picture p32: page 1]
Zahnriemenscheibe 16-5M-09 Artikel 410477 Zahnriemen24.de; Zahnriemenscheibe 30-5M-09 Artikel 410485 Zahnriemen24.de; verwendeter Zahnriemen Gates POWERGRIP® GT3 350-5MGT-9 Artikel 313288, Zahnriemen24.de

Teilung: 5 mm | Länge: 350 mm | Breite: 9 mm

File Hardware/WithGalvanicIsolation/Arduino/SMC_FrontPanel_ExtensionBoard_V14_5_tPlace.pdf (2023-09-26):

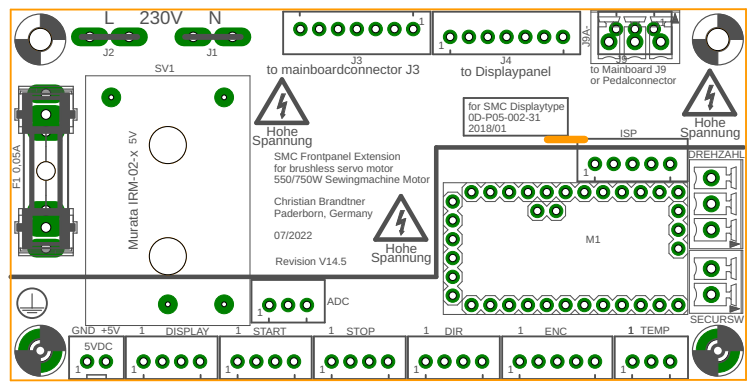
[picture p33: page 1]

SMC Frontpanel Extension
for brushless servo motor 550/750W Sewingmachine Motor Christian Brandtner Paderborn, Germany

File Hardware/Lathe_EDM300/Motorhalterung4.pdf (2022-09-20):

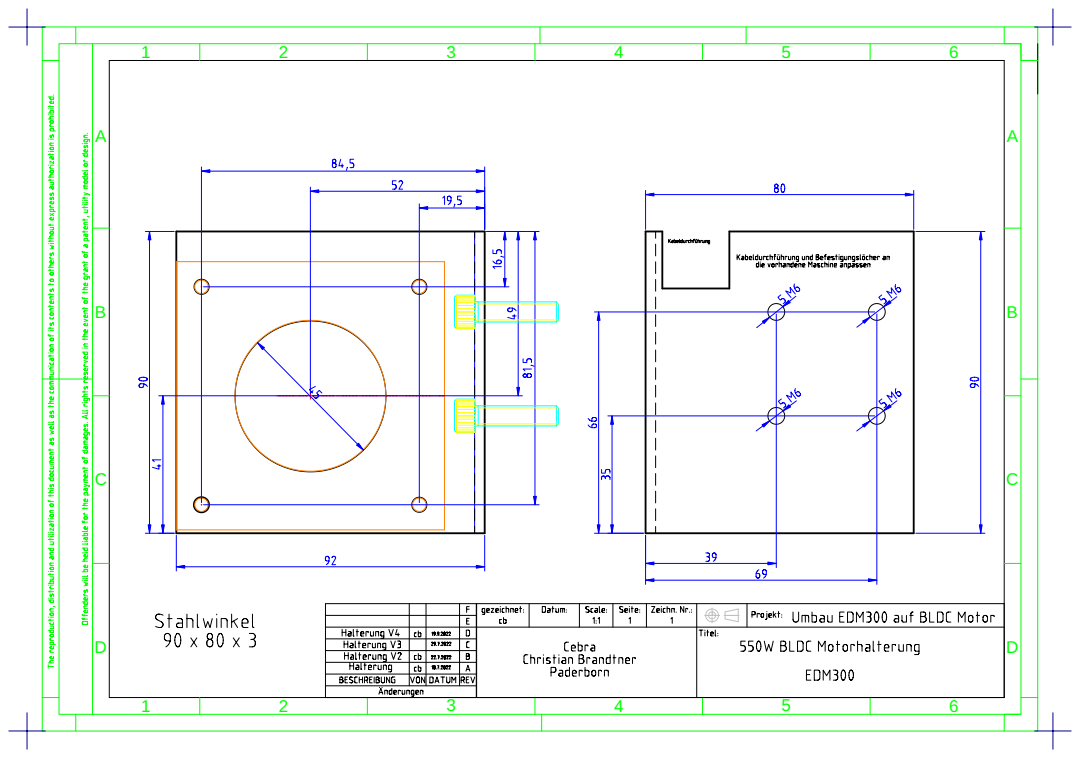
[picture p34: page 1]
6 ABCD; ABCD 1

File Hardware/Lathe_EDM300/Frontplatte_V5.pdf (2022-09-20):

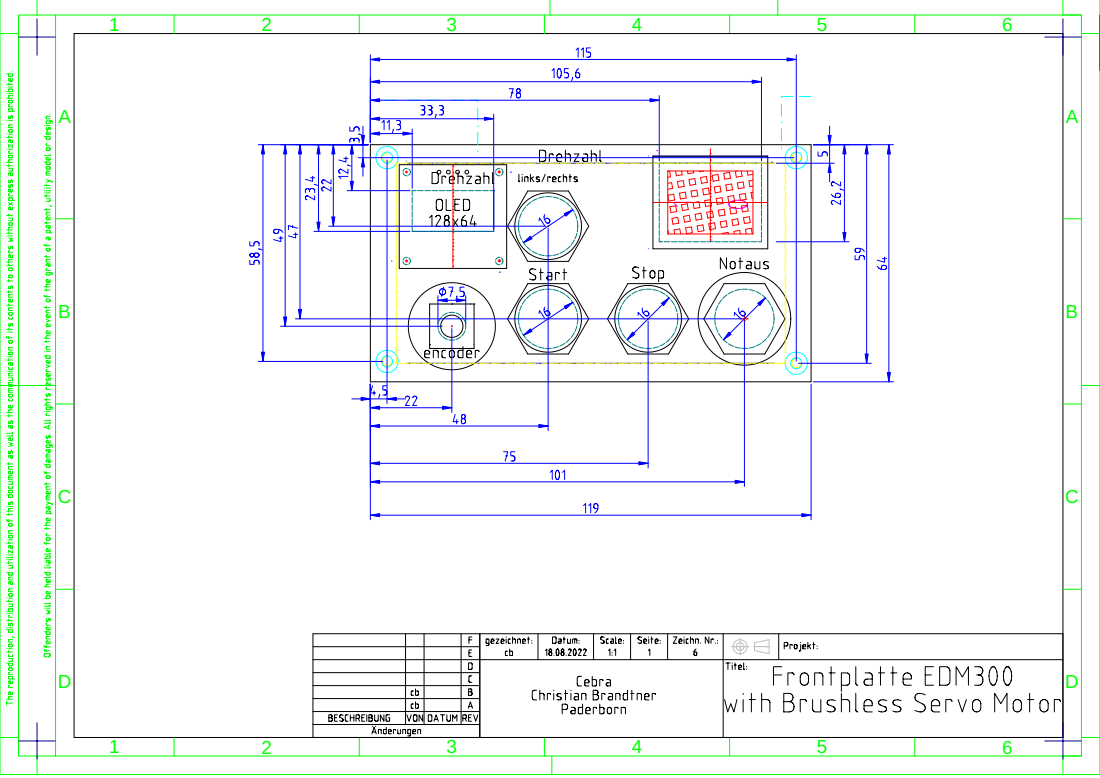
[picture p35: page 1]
6 ABCD; ABCD 1

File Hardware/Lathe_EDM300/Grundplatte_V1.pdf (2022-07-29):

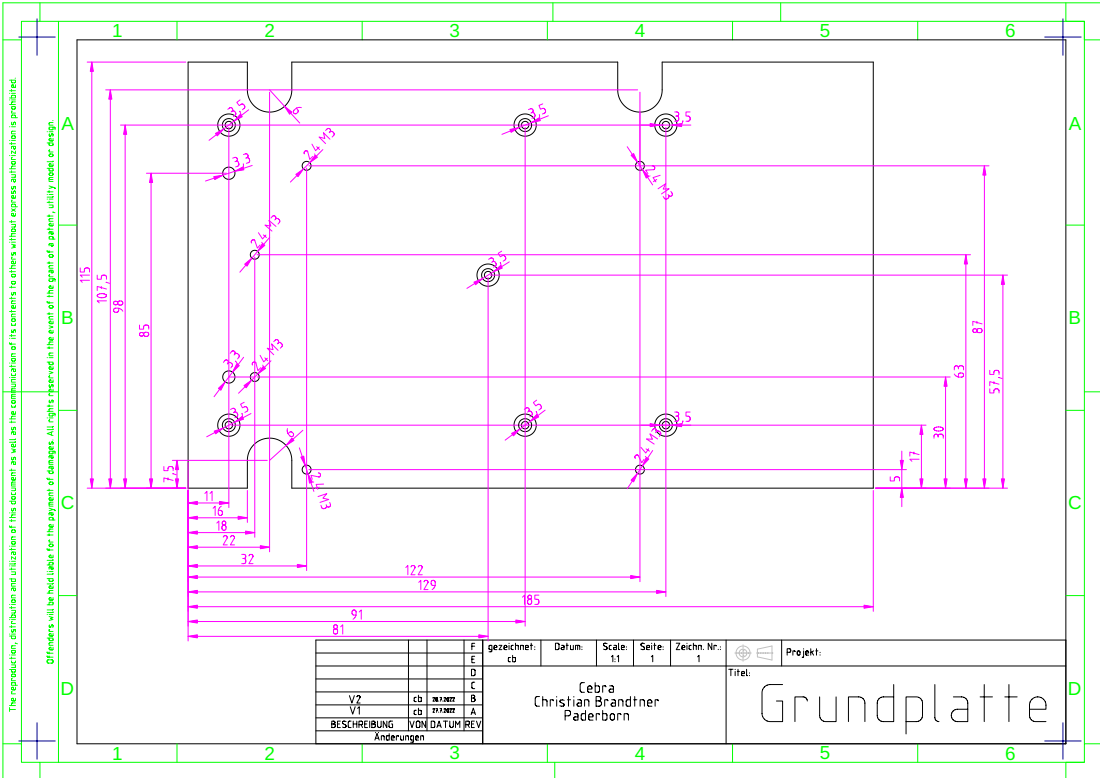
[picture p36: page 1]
6 ABCD; ABCD 1

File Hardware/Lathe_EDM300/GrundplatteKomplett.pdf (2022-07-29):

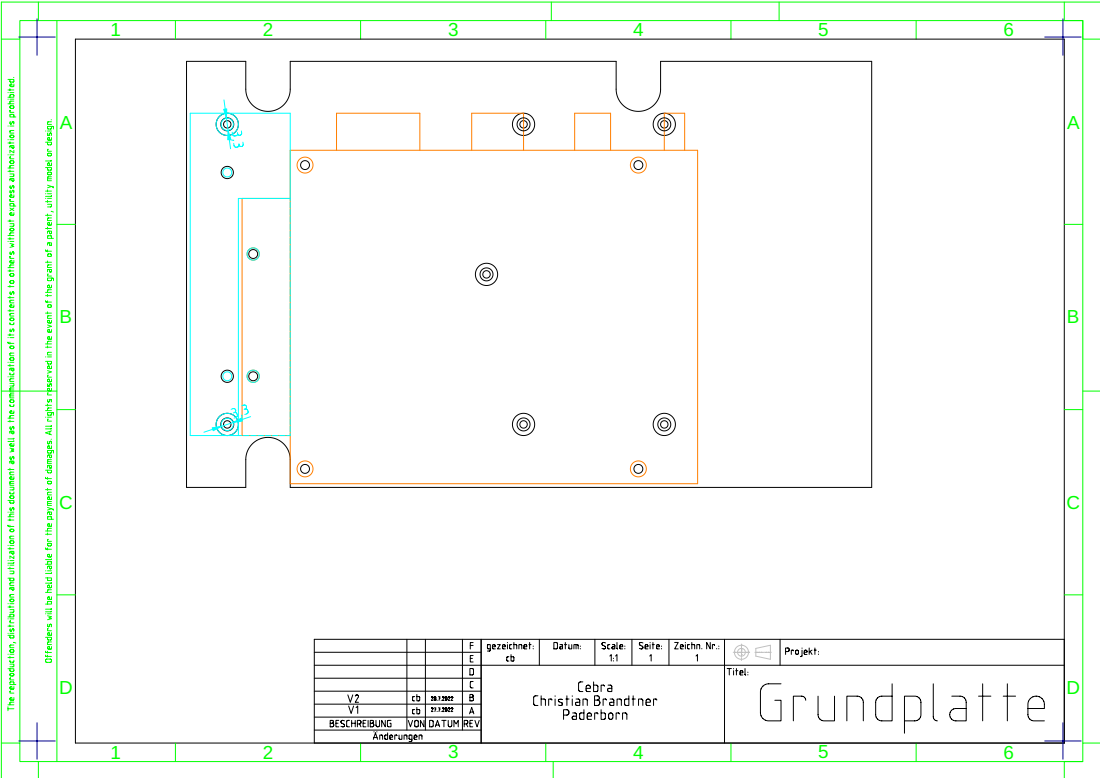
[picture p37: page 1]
6 ABCD; ABCD 1

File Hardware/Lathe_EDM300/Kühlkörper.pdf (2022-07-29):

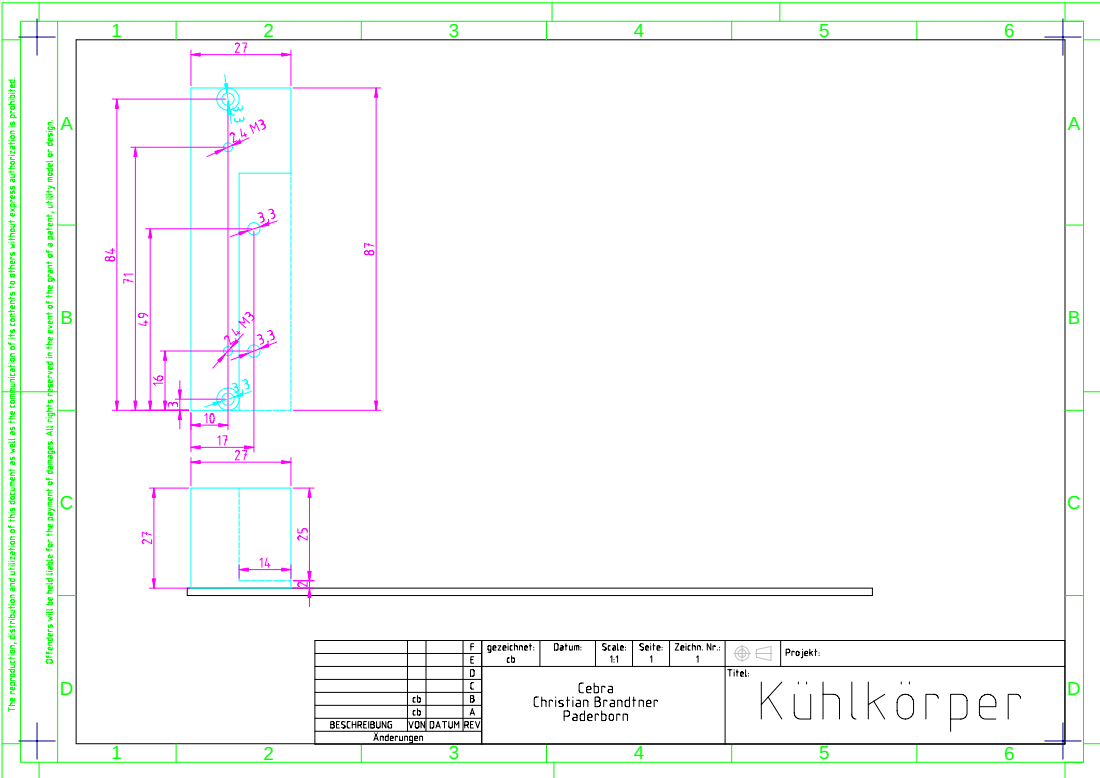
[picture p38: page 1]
6 ABCD; ABCD 1

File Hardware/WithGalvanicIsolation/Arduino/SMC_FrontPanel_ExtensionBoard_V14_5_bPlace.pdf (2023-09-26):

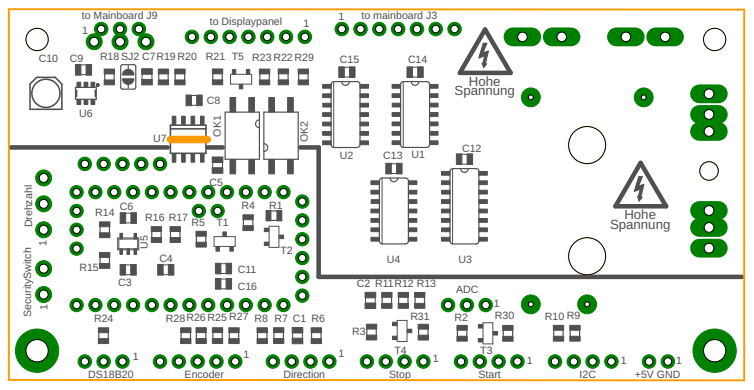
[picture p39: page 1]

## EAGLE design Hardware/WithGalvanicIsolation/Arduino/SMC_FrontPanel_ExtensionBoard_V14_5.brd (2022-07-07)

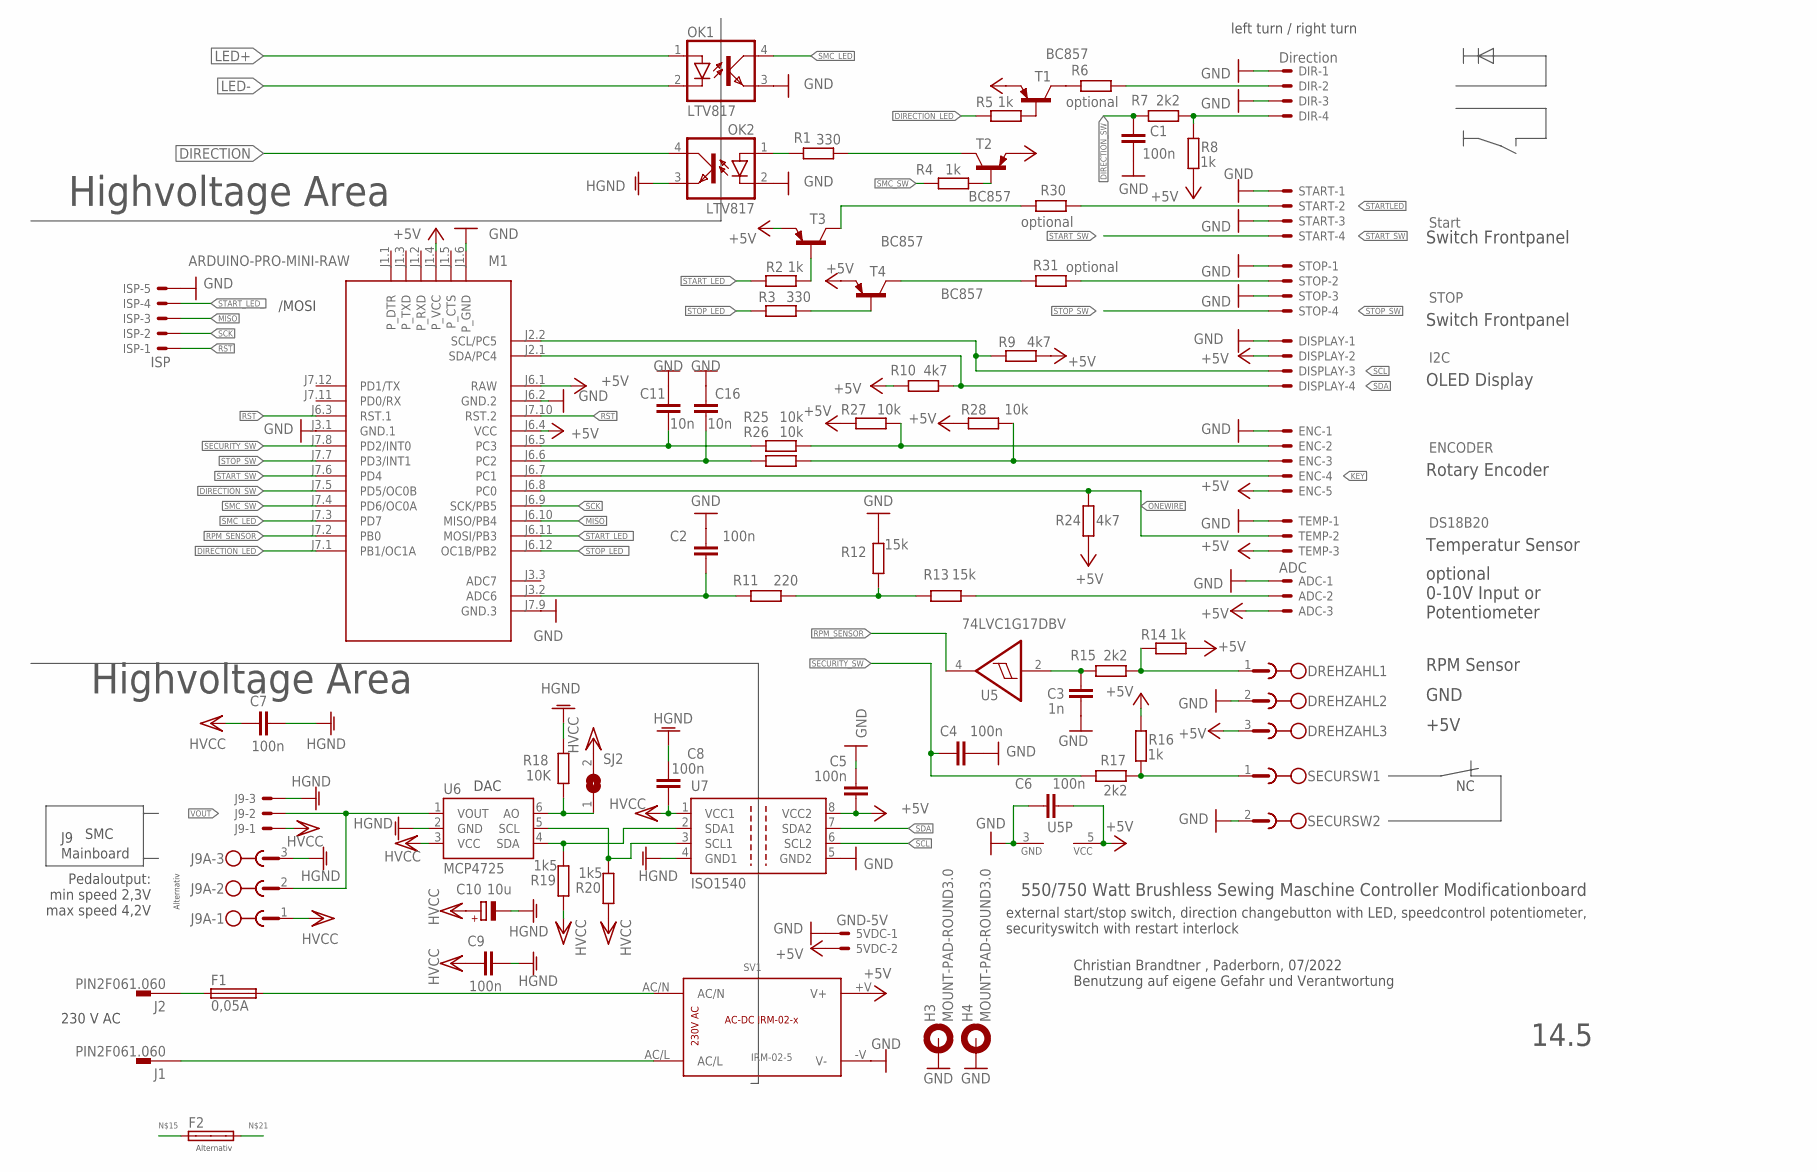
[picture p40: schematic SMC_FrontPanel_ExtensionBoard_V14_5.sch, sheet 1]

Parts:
5VDC: GND-5V; JST-XH-02-PACKAGE-ROUND-PAD
ADC: ADC; JST-XH-03-PACKAGE-ROUND-PAD
C1, C2, C4, C5, C6, C7, C8, C9: 100n; C0805
C3: 1n; C0805
C10: 10u; 153CLV-0405
C11, C16: 10n; C0805
DIR: Direction; JST-XH-04-PACKAGE-ROUND-PAD
DISPLAY: I2C; JST-XH-04-PACKAGE-ROUND-PAD
DREHZAHL: MCV_1.5/3/-G-3.5; 1843619
ENC: ENCODER; JST-XH-05-PACKAGE-ROUND-PAD
F1: 0,05A; MTA501100
F2: SHK20L
H3, H4: MOUNT-PAD-ROUND3.0; 3,0-PAD
ISP: ISP; JST-XH-05-PACKAGE-ROUND-PAD
J1, J2: PIN2F061.060; F061.060
J9: JST-XH-03-PIN-ROUND-PAD; JST-XH-03-PACKAGE-ROUND-PAD
J9A-: MCV_1.5/3/-G-3.5; 1843619
M1: ARDUINO-PRO-MINI-RAW; ARDUINO-PRO-MINI
OK1, OK2: LTV817; SMD4-7
R1, R3: 330; R0805
R2, R4, R5, R8, R14, R16: 1k; R0805
R6, R30, R31: optional; R0805
R7, R15, R17: 2k2; R0805
R9, R10, R24: 4k7; R0805
R11: 220; R0805
R12, R13: 15k; R0805
R18: 10K; R0805
R19, R20: 1k5; R0805
R25, R26, R27, R28: 10k; R0805
SECURSW: MCV_1,5/2-G-3,5; 1843606
SJ2: SJ
START: Start; JST-XH-04-PACKAGE-ROUND-PAD
STOP: STOP; JST-XH-04-PACKAGE-ROUND-PAD
SV1: IRM-02-5; IRM-02-X
T1, T2, T3, T4: BC857; SOT23-BEC
TEMP: DS18B20; JST-XH-03-PACKAGE-ROUND-PAD
U5: 74LVC1G17DBV; SOT23-5
U6: MCP4725; SOT23-6
U7: ISO1540; SO-08

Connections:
+5V: 5VDC.2, ADC.3, C5.1, C6.1, DISPLAY.2, DREHZAHL.3, ENC.5, M1.J1.4 (P_VCC), M1.J6.1 (RAW), M1.J6.4 (VCC), R8.2, R9.1, R10.1, R14.1, R16.1, R24.2, R27.1, R28.1, SV1.+V (V+), T1.E, T2.E, T3.E, T4.E, TEMP.3, U5.5 (VCC), U7.8 (VCC2)
ADC_POTI: C2.1, M1.J3.2 (ADC6), R11.1
DIRECTION: OK2.4 (COL); also elsewhere on the board
DIRECTION_LED: M1.J7.1 (PB1/OC1A), R5.2
DIRECTION_SW: C1.2, M1.J7.5 (PD5/OC0B), R7.1
GND: 5VDC.1, ADC.1, C1.1, C2.2, C3.1, C4.2, C5.2, C6.2, C11.2, C16.2, DIR.1, DIR.3, DISPLAY.1, DREHZAHL.2, ENC.1, H3.B3,0, H4.B3,0, ISP.5, M1.J1.6 (P_GND), M1.J3.1 (GND.1), M1.J6.2 (GND.2), M1.J7.9 (GND.3), OK1.3 (EMIT), OK2.2 (C), R12.2, SECURSW.2, START.1, START.3, STOP.1, STOP.3, SV1.-V (V-), TEMP.1, U5.3 (GND), U7.5 (GND2)
HGND: C7.1, C8.2, C9.1, C10.-, J9.3, J9A-.3, OK2.3 (EMIT), R18.1, U6.2 (GND), U7.4 (GND1); also elsewhere on the board
HVCC: C7.2, C8.1, C9.2, C10.+, J9.1, J9A-.1, R19.2, R20.2, SJ2.2, U6.3 (VCC), U7.1 (VCC1); also elsewhere on the board
KEY: ENC.4, M1.J6.7 (PC1)
LED+: OK1.1 (A); also elsewhere on the board
LED-: OK1.2 (C); also elsewhere on the board
MISO: ISP.3, M1.J6.10 (MISO/PB4)
unnamed: OK2.1 (A), R1.2
unnamed: R1.1, T2.C
unnamed: R30.1, START.2
unnamed: R2.1, T3.B
unnamed: C3.2, R15.1, U5.2 (I)
unnamed: R3.1, T4.B
unnamed: R18.2, SJ2.1, U6.6 (AO)
unnamed: F1.1, F2.1A, J2.A1, J2.A2
unnamed: DREHZAHL.1, R14.2, R15.2
unnamed: R16.2, R17.2, SECURSW.1
unnamed: R31.2, T4.C
unnamed: R11.2, R12.1, R13.2
unnamed: ADC.2, R13.1
unnamed: F1.2, F2.2A, SV1.AC/N
unnamed: J1.A1, J1.A2, SV1.AC/L
unnamed: R6.2, T1.C
unnamed: DIR.2, R6.1
unnamed: R5.1, T1.B
unnamed: R4.1, T2.B
unnamed: R20.1, U6.5 (SCL), U7.3 (SCL1)
unnamed: DIR.4, R7.2, R8.1
unnamed: C16.1, M1.J6.6 (PC2), R26.1
unnamed: C11.1, M1.J6.5 (PC3), R25.1
unnamed: ENC.2, R25.2, R27.2
unnamed: ENC.3, R26.2, R28.2
unnamed: R31.1, STOP.2
ONEWIRE: M1.J6.8 (PC0), R24.1, TEMP.2
RPM_SENSOR: M1.J7.2 (PB0), U5.4 (O)
RST: ISP.1, M1.J6.3 (RST.1), M1.J7.10 (RST.2)
SCK: ISP.2, M1.J6.9 (SCK/PB5)
SCL: DISPLAY.3, M1.J2.2 (SCL/PC5), R9.2, U7.6 (SCL2)
SDA: DISPLAY.4, M1.J2.1 (SDA/PC4), R10.2, U7.7 (SDA2)
SDA_HV: R19.1, U6.4 (SDA), U7.2 (SDA1)
SECURITY_SW: C4.1, M1.J7.8 (PD2/INT0), R17.1
SMC_LED: M1.J7.3 (PD7), OK1.4 (COL)
SMC_SW: M1.J7.4 (PD6/OC0A), R4.2
STARTLED: R30.2, T3.C
START_LED_: ISP.4, M1.J6.11 (MOSI/PB3), R2.2
START_SW: M1.J7.6 (PD4), START.4
STOP_LED_: M1.J6.12 (OC1B/PB2), R3.2
STOP_SW: M1.J7.7 (PD3/INT1), STOP.4
VOUT: J9.2, J9A-.2, U6.1 (VOUT)

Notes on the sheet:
left turn / right turn
SMC
Pedaloutput: min speed 2,3V max speed 4,2V
DAC
Highvoltage Area
14.5
OLED Display
Rotary Encoder
Temperatur Sensor
Switch Frontpanel
optional 0-10V Input or Potentiometer
RPM Sensor
550/750 Watt Brushless Sewing Maschine Controller Modificationboard
external start/stop switch, direction changebutton with LED, speedcontrol potentiometer, securityswitch with restart interlock
Christian Brandtner , Paderborn, 07/2022 Benutzung auf eigene Gefahr und Verantwortung
230 V AC
J9 Mainboard
+5V
GND
Alternativ
/MOSI

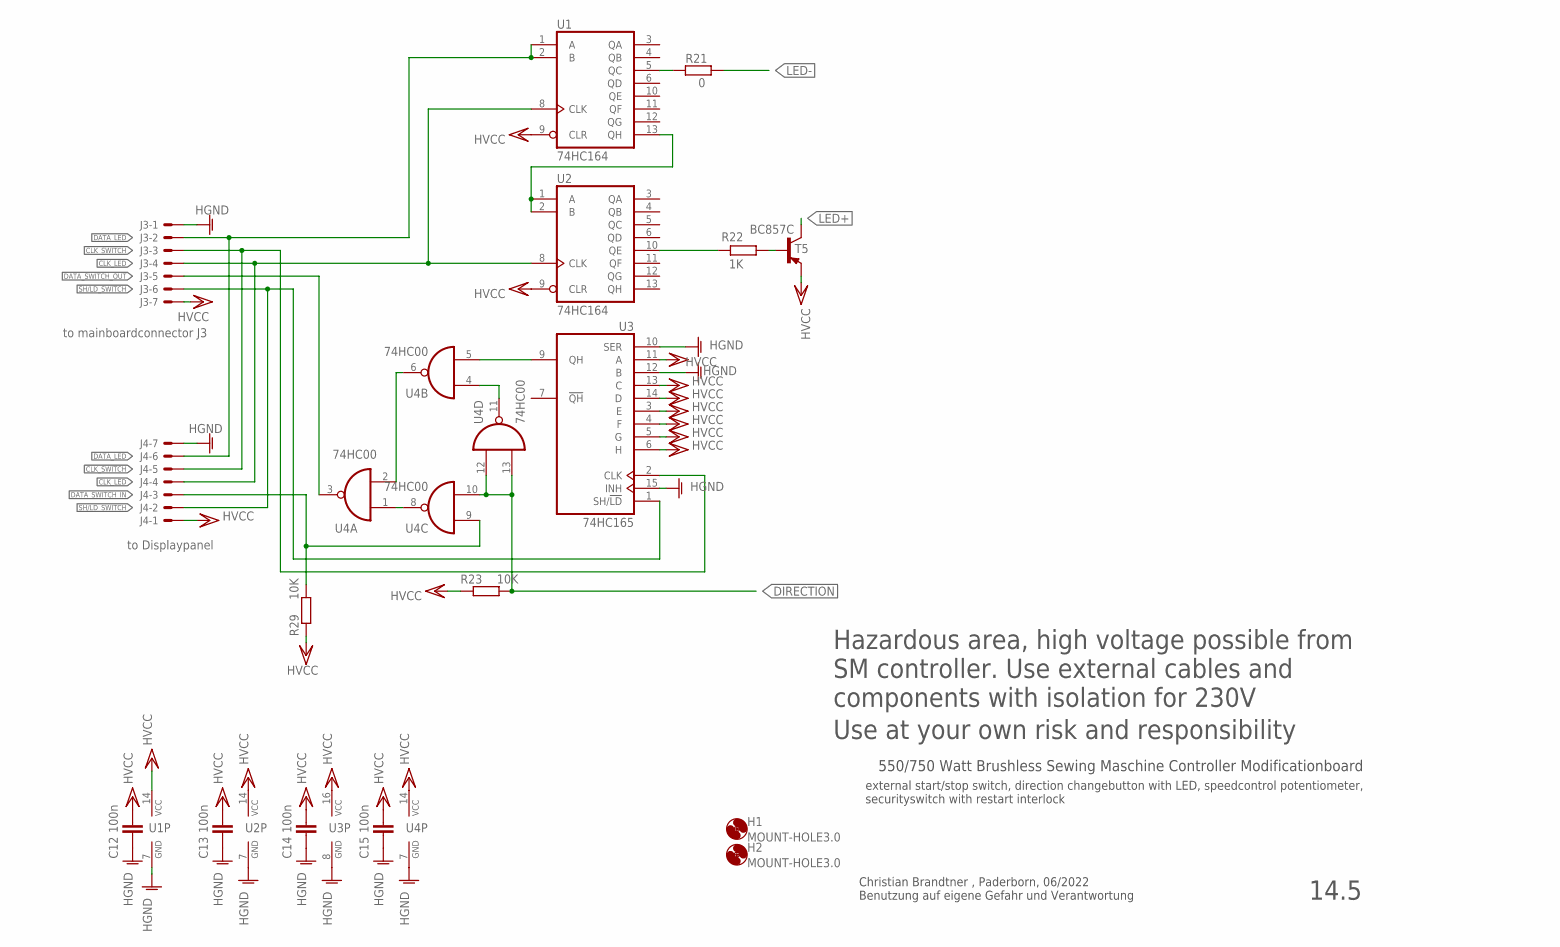
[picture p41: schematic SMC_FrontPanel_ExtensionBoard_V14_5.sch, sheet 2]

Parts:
C12, C13, C14, C15: 100n; C0805
H1, H2: MOUNT-HOLE3.0; 3,0
J3: to mainboardconnector J3; JST-XH-07-PACKAGE-ROUND-PAD
J4: to Displaypanel; JST-XH-07-PACKAGE-ROUND-PAD
R21: 0; R0805
R22: 1K; R0805
R23, R29: 10K; R0805
T5: BC857C; SOT23-BEC
U1, U2: 74HC164; SO14
U3: 74HC165; SO16
U4: 74HC00; SO14

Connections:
CLK_LED: J3.4, J4.4, U1.8 (CLK), U2.8 (CLK)
CLK_SWITCH: J3.3, J4.5, U3.2 (CLK)
DATA_LED: J3.2, J4.6, U1.1 (A), U1.2 (B)
DATA_SWITCH_IN: J4.3, R29.1, U4.9 (I0)
DATA_SWITCH_OUT: J3.5, U4.3 (O)
DIRECTION: R23.1, U4.10 (I1), U4.12 (I0), U4.13 (I1); also elsewhere on the board
G: U1.13 (QH), U2.1 (A), U2.2 (B)
HGND: C12.1, C13.1, C14.1, C15.1, J3.1, J4.7, U1.7 (GND), U2.7 (GND), U3.8 (GND), U3.10 (SER), U3.12 (B), U3.15 (INH), U4.7 (GND); also elsewhere on the board
HVCC: C12.2, C13.2, C14.2, C15.2, J3.7, J4.1, R23.2, R29.2, T5.E, U1.9 (CLR), U1.14 (VCC), U2.9 (CLR), U2.14 (VCC), U3.3 (E), U3.4 (F), U3.5 (G), U3.6 (H), U3.11 (A), U3.13 (C), U3.14 (D), U3.16 (VCC), U4.14 (VCC); also elsewhere on the board
LED+: T5.C; also elsewhere on the board
LED-: R21.2; also elsewhere on the board
unnamed: R22.1, T5.B
unnamed: R21.1, U1.5 (QC)
unnamed: U3.9 (QH), U4.5 (I1)
unnamed: U4.2 (I1), U4.6 (O)
unnamed: U4.1 (I0), U4.8 (O)
unnamed: U4.4 (I0), U4.11 (O)
unnamed: R22.2, U2.10 (QE)
SH/LD_SWITCH: J3.6, J4.2, U3.1 (SH/!LD)

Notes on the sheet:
550/750 Watt Brushless Sewing Maschine Controller Modificationboard
external start/stop switch, direction changebutton with LED, speedcontrol potentiometer, securityswitch with restart interlock
Hazardous area, high voltage possible from SM controller. Use external cables and components with isolation for 230V
Christian Brandtner , Paderborn, 06/2022 Benutzung auf eigene Gefahr und Verantwortung
14.5
Use at your own risk and responsibility

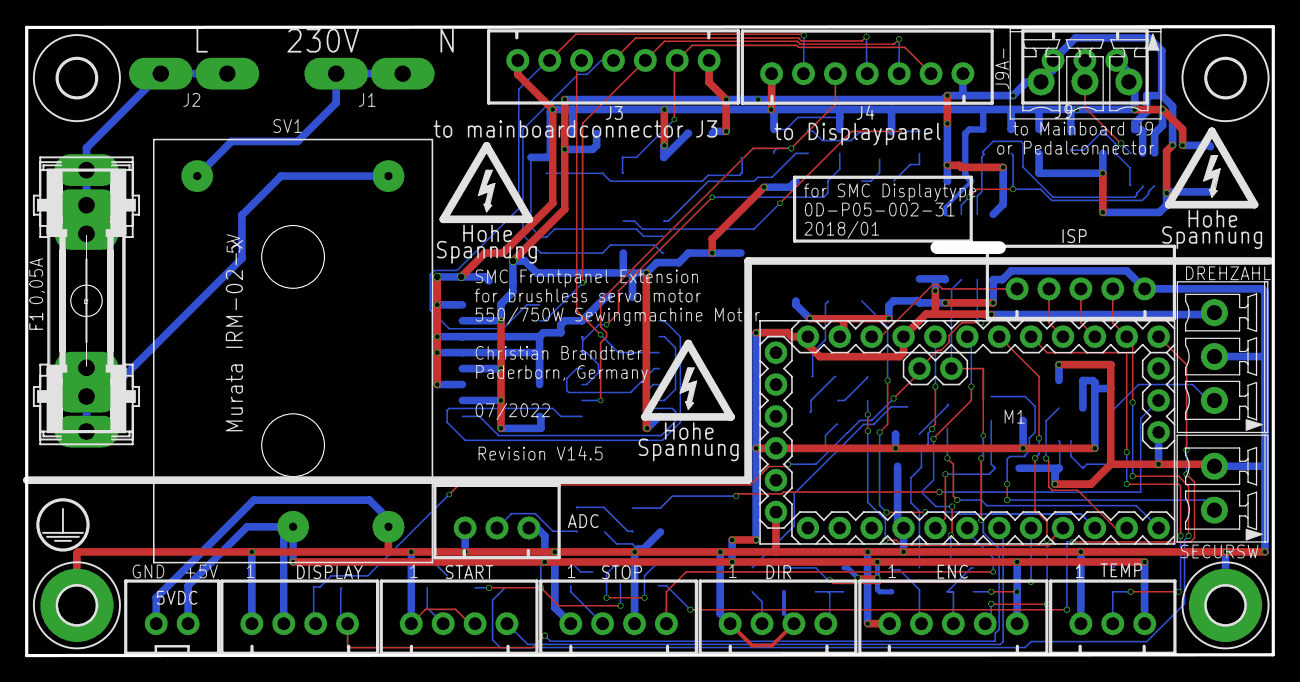
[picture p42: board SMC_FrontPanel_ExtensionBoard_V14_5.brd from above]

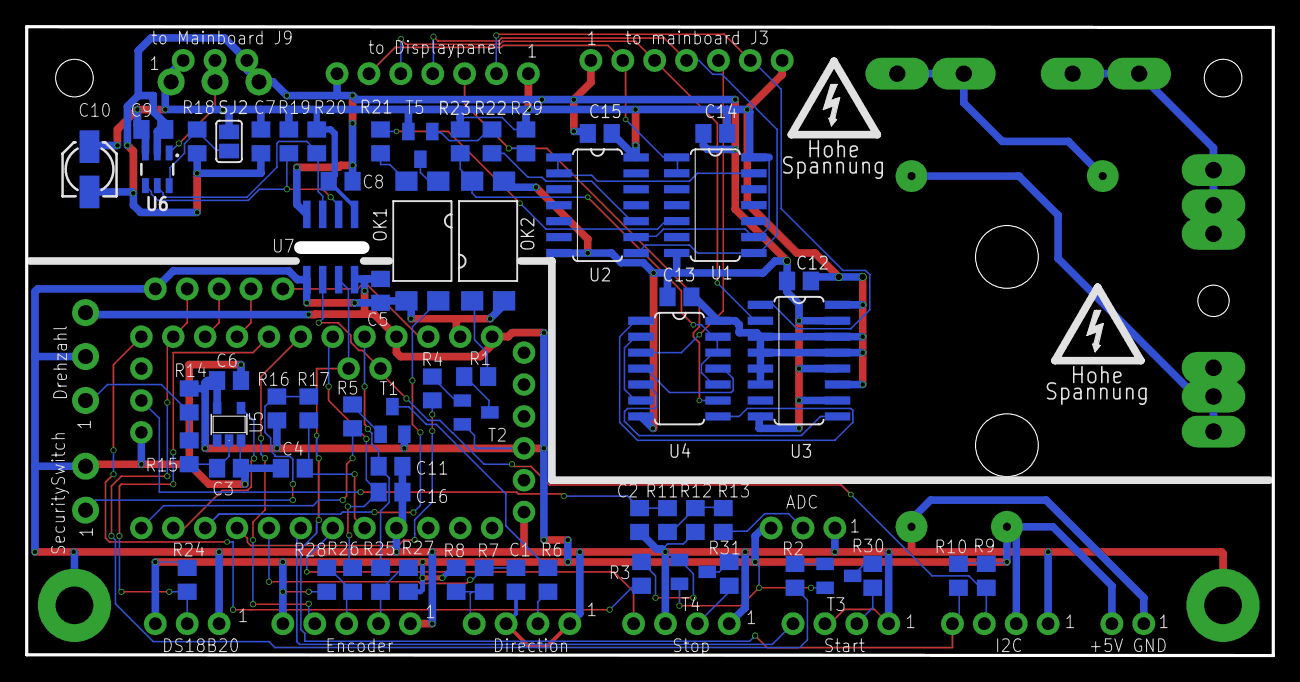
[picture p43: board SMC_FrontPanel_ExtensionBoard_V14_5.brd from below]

Board: 2 copper layers, 99.3 x 50.1 mm, 93 parts (62 on the bottom side), 68 nets.

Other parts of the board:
U$53, U$54, U$57: HIGHVOLT1_TOP
U$55, U$56: HIGHVOLT1_BOT
U$58: SCHUTZLEITER

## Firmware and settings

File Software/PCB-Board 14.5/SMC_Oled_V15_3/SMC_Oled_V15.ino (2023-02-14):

#define _SMC_OLED_V14_

/*****************************************************************************
 *   Copyright (C) 2023 Christian "Cebra" Brandtner, brandtner@brandtner.net*
 *                                                                          *
 *   This program is free software; you can redistribute it and/or modify   *
 *   it under the terms of the GNU General Public License as published by   *
 *   the Free Software Foundation; either version 2 of the License.         *
 *                                                                          *
 *   This program is distributed in the hope that it will be useful,        *
 *   but WITHOUT ANY WARRANTY; without even the implied warranty of         *
 *   MERCHANTABILITY or FITNESS FOR A PARTICULAR PURPOSE.  See the          *
 *   GNU General Public License for more details.                           *
 *                                                                          *
 *   You should have received a copy of the GNU General Public License      *
 *   along with this program; if not, write to the                          *
 *   Free Software Foundation, Inc.,                                        *
 *   59 Temple Place - Suite 330, Boston, MA  02111-1307, USA.              *
 *                                                                          *
 *                                                                          *
 *   Credits to:                                                            *
 *		Marc Schönfleisch and his Arduino_Spot_Welder						*
 *		(https://github.com/KaeptnBalu/Arduino_Spot_Welder_V4)				*
 *																			*
 *	Sourcecode location:													*
 *																			*
 *		https://github.com/ChristianBrandtner		 						*
 *																			*
 ****************************************************************************/




/************************************************************************************************
 *
 * my development environment:
 *
 * Eclipse IDE for C/C++ Developers, Version: 2022-12 (4.26.0)
 * Sloeber, the Eclipse Arduino IDE (plugin version) 4.4.1
 *
 *
 *
 * !!!!!! Important   USE Libraries in utils folder!!!!!!!
 *  there are changes compared to the original Arduino Libraries
 *
 *
 *
 ***********************************************************************************************/



/************************************************************************************************
 * Flashing program to Arduino
 *
 * Linux in terminal window:
 *
 * avrdude -patmega328p -carduino -P/dev/ttyUSB0 -b115200 -D -Uflash:w:SMC_Oled_V15_3.hex:i
 *
 * Windows in commandline window (CMD eg. DOS window):
 *
 * avrdude -patmega328p -carduino -PCOM1 -b115200 -D -Uflash:w:SMC_Oled_V15_3.hex:i
 *
 ***********************************************************************************************/



/************************************************************************************************
 * It is only necessary if the bootloader was overwritten
 * Bootloader flash, Important use optiboot bootloader!!, we need all memory until 32256
 * avrdude -pm328P -cstk500v2 -P/dev/ttyUSB0 -b115200 -u
 * -Uflash:w:optiboot_atmega328.hex:a -Ulfuse:w:0xFF:m -Uhfuse:w:0xDE:m -Uefuse:w:0xFD:m -Ulock:w:0x3F:m
 ************************************************************************************************/







//############################################################################
//# HISTORY  SMC_Oled_V15_2.ino
//#
//# 17.01.2023 cebra
//# - add:
//# - chg: MIN_ENCSLOTS = 4	(für den Hallsensoe werden min. 4 Magnete benötigt)
//# - fix: save display orientation in bootmenu
//# - del:
//############################################################################


/***********************************************************************************************//**
 *              Menu and display Screen Descriptions.
 *              The main screen is accessed by a normal device boot.
 *              The system menu is acessed by helding the encoder button;
 *
 +----------------+  MAIN SCREEN
 |   Status Line  |  Temperature and Status information
 |----------------|
 | SPEED          |  Rotation speed
 | rotation       |  and direction of rotation (L or R)
 |   calc. Speed  |  calculated speed high shiftes gear, low shifted gear,  motor
 +----------------+

 +----------------+  SYSTEM MENU
 |   Systemmenu   |  menu label
 |----------------|
 |   gear / ENC   |  raise the gear / encoder setting screen
 |   temperatur   |  raise the temperature setting screen
 |   exit		  |  exit the System menu
 +----------------+

 +----------------+  GEAR/ENCODER SETTINGS
 | gear/encoder se|  Menu label
 |----------------|
 |    gears       |  raise the gears setting screen
 |    # slots     |  raise the number of encoderslots setting screen
 |     Exit       |  Exit to the System Menu screen
 +----------------+


 +----------------+  GEARRATIO SETTINGS
 | gear ratio set |  Menu label
 |----------------|
 |    driveRatio  |  ratio of the motor belt drive
 |    speed  Hi   |  ratio of the high speed gear shifter
 |    speed  Lo   |  ratio of the low speed gear shifter
 +----------------+

 +----------------+  ENCODER SETTINGS
 | encoder slots  |  Menu label
 |----------------|
 |      		  |  Depends of used encoder solution, optical or hallsensor
 | Number of slots|  number of slots or magnets
 |                |
 +----------------+

 +----------------+  TEMPERATURE SETTINGS
 | Temperature Set|  Menu label
 |----------------|
 | Temp.Alarm     |	 temperature threshold	for overheating of the SMC Controller, default 65 centigrade
 | celsius		  |  Unit of measurement, celsius/fahrenheit
 | Exit           |
 +----------------+




    The system screen is accessed by booting the device with the encoder push button pressed.
    The screen allows changing of system settings. It is arranged as follows;

 +----------------+  SYSTEM MENU
 |    Display     |  toggle the Display orientation
 |    EEP Reset   |  !! EEPROM Reset to factory values !!
 |     Exit       |  Reboot
 +----------------+


 *//***********************************************************************************************/


#include <Arduino.h>
#include <SPI.h>
#include <Wire.h>
#include <avr/wdt.h>
#include <gfxfont.h>
#include <Adafruit_SSD1306.h>
#include <EEPROM.h>
#include <OneWire.h>
#include <DallasTemperature.h>
#include "ClickEncoder.h"
#include "MCP4725.h"
#include "TimedBlink.h"
#include "SMC_Oled_V15.h"

//************************************************************************************
// Integrate watchdog and switch off, is required for bootloader
//  !!must stay here on top!!

//--------------------------------------------------------------
void wdt_init(void) __attribute__((naked)) __attribute__((section(".init1")));

//--------------------------------------------------------------
void wdt_init(void)
{
    MCUSR = 0;
    wdt_disable();
    return;
}

//**********************************!!do not move this code!!**************************************************

// Machine states
enum states {

	ST_MAIN_SCREEN,    /**< Machine state: display main screen */
	ST_MAIN_SCREEN_CNT, /**< Machine state: display statistics */
	ST_MENU_SCREEN,    /**< Machine state: display menu screen */
	ST_CHANGE_DIR,    /**< Machine state: Motor change direction*/
	ST_WAIT_CHANGE_DIR, /**< Machine state: Wait change LED direction*/
	ST_DP4ON,			/**< Machine state: DP4 LED on*/
	ST_DP4OFF,			/**< Machine state: DP4 LED off*/
    ST_TEMP_HIGH,      /**< Machine state: high temperature */
	ST_SECURITYSTOP,	/**< Machine state: Security Switch Stop */
	ST_RPM_SCREEN,
	ST_GEARENC_MENU,
	ST_ENCDISC,			/**< Machine state: Encoderdisc slots */
	ST_TEMP_MENU,
	ST_GEAR_MENU,
	ST_RED_RATIO,
	ST_SET_C_F,
	ST_SET_HIGHTEMP,
	ST_SYSTEM_SCREEN,  /**< Machine state: display system screen */
	ST_SYSTEM_MENU,    /**< Machine state: display system menu */
	ST_SETTINGS_MENU,  /**< Machine state: display settings menu */
	ST_REBOOT_MENU,    /**< Machine state: display reboot menu */
	ST_INVERT_SCREEN,  /**< Machine state: display invert setting screen */

};

enum event {
	// Private machine events
	EV_NONE,           /**< Machine event: no pending event */
	EV_BTNCL,          /**< Machine event: button down */
	EV_BTNUP,          /**< Machine event: button released */
	EV_BTNDC,		   /**< Machine event: button double clicked */
	EV_BTNHD,		   /**< Machine event: button held*/
	EV_BTNOP,		   /**< Machine event: button open*/
	EV_DP4ON,		   /**< Machine event: DP4 Led an*/
	EV_DP4OFF,		   /**< Machine event: DP4 Led an*/

	EV_ENCUP,          /**< Machine event: encoder rotate right */
	EV_ENCDN,          /**< Machine event: encoder rotate left */



	// Public machine events
	EV_BOOTDN,         /**< Machine event: button pressed on boot */
	EV_TEMP_HIGH,      /**< Machine event: maximum temperature reached */
	EV_BTNSP,		   /**< Machine event: button stop*/
	EV_BTNST,		   /**< Machine event: button start*/
	EV_BTNDI,		   /**< Machine event: button direction*/
	EV_STOP				/**< Security Stop*/
};


enum error{
	ER_DISPLAY,			/**< Error event: Display I2C Error*/
	ER_DAC				/**< Error event: DAC I2C Error*/

};


/***************************************************************************************************
* Global program variables and objects                                                             *
***************************************************************************************************/

// Structures and objects
progData pData;                             /**< Program operating data */
Adafruit_SSD1306 display ( SCREEN_WIDTH , SCREEN_HEIGHT, &Wire, OLED_RESET, 800000L ); /**< OLED display object */

// Static variables
uint8_t mState         = ST_MAIN_SCREEN;    /**< Current machine state */
uint8_t TCelsius;                          /**< System temperature in celsius */
boolean sysMenu = false;             /**< In the system menu structure */
int16_t oldEncPos, encPos;
int16_t encDelta=0;
bool val_edited = false;				//	Flag für veränderte EEPROM Werte, danach save EEPROM
int16_t editdata;
float DAC_VAL;


int16_t MotorRotational_speed=100;    	/**< Motordrehzahl */
int16_t SpindleRotational_speed;   /**< Spindle Rotation Speed */

bool StartButton = false;
bool StopButton = false;
bool DirButton = false;
bool Runing = false;					// Motor läuft
bool Security_Switch_Closed = false;	// Securityswitch geschlossen
bool SMC_Dir_Led = false;				// Direction from SMC Display on/off (DP4)
bool BUT_Dir_Led = false;				// Direction Button LED  on/off
bool SYS_ERROR = false;			   //
bool DisplayError = false;
bool DAC_Error = false;
bool EEPROM_Error = false;
bool SMC_Error = false;					// Keine kommunkation vom SMC (DP4-Signal)
bool TempSensor_Error = false;
bool ChangeDir_Button = false;			// Flag wenn Dir Button in Bearbeitung ist
volatile boolean thisDP4State;


volatile unsigned long lastDP4 = 0;

// Volatile variables - will be changed by the ISR
volatile unsigned long lastActiveTime;
volatile uint8_t mEvent;          /**< Current pending machine event */


// Setup a oneWire instance to communicate with any OneWire devices (not just Maxim/Dallas temperature ICs)
OneWire oneWire(ONE_WIRE_BUS);

// Pass our oneWire reference to Dallas Temperature.
DallasTemperature sensors(&oneWire);

// arrays to hold device address
DeviceAddress insideThermometer;

MCP4725 dac(DAC_ADRESS);

ClickEncoder Encoder = ClickEncoder(ENCODER_PINA,ENCODER_PINB,ENCODER_BTN,ENCODER_STEPS_PER_NOTCH);


TimedBlink DirectionLED(DIR_LED_PIN,true); 		// LED active low
TimedBlink StopLED(STOP_LED_PIN,true);
TimedBlink StartLED(START_LED_PIN,true);



int  resolution = 9;
unsigned long lastTempRequest = 0;
float SensorTemperature = 0.0;

int  idle = 0;


/***************************************************************************************************
* Debouncing in Timer ISR                                                                                    *
***************************************************************************************************/
volatile uint8_t key_state = 0;                      // debounced and inverted key state:
                                            		 // bit = 1: key pressed
volatile uint8_t DP4 = HIGH;						// Zustand der DP4 Dezimalpunktes der SMC Anzeige
volatile uint8_t DP4State = HIGH;					//
volatile uint8_t old_DP4State = HIGH;
volatile uint16_t DIR_Timer =0;						// Timerout für Richtungsumschaltung

volatile bool count330ms = false;					// neue Zählung fertig;
volatile uint16_t CountArray[3];

volatile uint8_t work_key_state = 0;
volatile uint8_t key_press = 0;                      // key press detect
volatile uint8_t key_release =0;						// key release detect
volatile uint8_t key_long  = 0;                      // key long press
volatile uint8_t key_rpt   = 0;                      // key repeat
volatile uint8_t key_lrpt  = 0;                      // key long press and repeat
volatile uint8_t key_rpts  = 0;                      // key long press and speed repeat
volatile uint8_t repeat_speed = 0;

volatile uint16_t debounceinterval = 0;

volatile uint8_t debouncestate = 0;

//**** RPM
#define BUF_SIZE	16
#define F_CPU2		16000000UL
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
void loop()
{

	// The state machine is run every loop cycle - as fast as possible.

	stateMachine();

	DirectionLED.blink();
	StopLED.blink();
	StartLED.blink();

	updateEeprom(false);



}




/***************************************************************************************************
* State Machine                                                                                    *
***************************************************************************************************/
/**
 *  \brief  Implementation of state machine.
 */

// This entire state machine is legacy code that has been much modified and added to. It is
// somewhat of a "dog's breakfast" and really is in need of a complete rewrite. Even I have
// difficulty following it and modifications that work are a pleasant surprise - JFF.

void stateMachine() {
	char str[5];
	static uint8_t selectedMenu       = 0;
	static uint8_t selectedMainMenu   = 0;
	static uint8_t selectedSubMenu    = 0;


	// Scan for events - the event queue length is one.

	// Process any public boot events. These events are the highest priority
	// and must be processed before any of the private events.
	if ( mEvent == EV_BOOTDN ) {			// sofort nach dem Booten
		mState = ST_SYSTEM_SCREEN;
		mEvent = EV_NONE;

	}
	else
	{

		// Search for and process any private events. Pulse Activated

		checkEncoderEvent();
		checkForBtnEvent();
		checkForDP4Event();
		checkTemperatur();

		switch (mEvent) {

		case EV_BTNST:					// Start Button gedrückt

			if (!sysMenu)
			{
				if (Security_Switch_Closed & !Runing & !DAC_Error)
				{
					StartLED.Off();
					StopLED.On();

					Runing = true;
					encDelta = 0;
					SetDrehzahl(MotorRotational_speed);

				}
			}
			mEvent = EV_NONE;
			break;

		case EV_BTNSP:					// Stop Button gedrückt
			if (!sysMenu)
			{
				if (Security_Switch_Closed && Runing)
				{
					SetDrehzahl(HALT);
					StartLED.On();
					StopLED.Off();
					Runing = false;
				}
			}

			mEvent = EV_NONE;
			break;

		case EV_BTNDI:					// Direction Button gedrückt

			if (!sysMenu) if (!Runing) mState = ST_CHANGE_DIR;

			mEvent = EV_NONE;
			break;


		case EV_DP4ON:					// DP4 vom SMC auf Low gesetzt, DP4 leuchtet

			if (!sysMenu) mState = ST_DP4ON;
			mEvent = EV_NONE;
			break;

		case EV_DP4OFF:					// DP4 vom SMC auf High gesetzt, DP4 ist aus

			if (!sysMenu) mState = ST_DP4OFF;
			mEvent = EV_NONE;
			break;

		case EV_TEMP_HIGH:

			if (!sysMenu) mState = ST_TEMP_HIGH;

			mEvent = EV_NONE;
			break;

		case EV_STOP:
			if (!sysMenu)
			{
				Security_Switch_Closed = false;
				Runing = false;
				SetDrehzahl(STOP);				// sofort Motor abschalten
				StopLED.blink(200,200);
				StartLED.Off();

				if (!sysMenu) mState = ST_SECURITYSTOP;
			}
			mEvent = EV_NONE;
			break;

		case EV_BTNUP:

			if (mState != ST_REBOOT_MENU) mEvent = EV_NONE;

			break;



		}
	}

	// Machine states
	switch ( mState ) {


  // Over temperature state. Entered by receiving a high temperature event,
  // this state can be exited by clicking the rotary encoder
  case ST_TEMP_HIGH:

    if ( mEvent == EV_BTNCL ) mState = sysMenu ? ST_SYSTEM_SCREEN : ST_MAIN_SCREEN;
    displayHighTemperature();
    mEvent = EV_NONE;
    break;    

    // Over temperature state. Entered by receiving a high temperature event,
    // this state can be exited by clicking the rotary encoder
    case ST_SECURITYSTOP:

      if ( mEvent == EV_BTNCL ) mState = sysMenu ? ST_SYSTEM_SCREEN : ST_MAIN_SCREEN;
      displaySecurityStop();
      if (Security_Switch_Closed)
    	  {
    	  mState = ST_MAIN_SCREEN_CNT;
    	  displayMainScreen( false );
    	  StopLED.blinkOff();


    	  }

      mEvent = EV_NONE;
      break;

	case ST_DP4ON:

		DirectionLED.On();

		mEvent = EV_NONE;
		if (ChangeDir_Button) mState = ST_WAIT_CHANGE_DIR;
		else
		{
			mState = ST_MAIN_SCREEN_CNT;
			displayMainScreen(false);
		}

		break;

	case ST_DP4OFF:

		DirectionLED.Off();

		mEvent = EV_NONE;
		if (ChangeDir_Button) mState = ST_WAIT_CHANGE_DIR;
		else
		{
			mState = ST_MAIN_SCREEN_CNT;
			displayMainScreen(false);
		}

		break;

	case ST_WAIT_CHANGE_DIR:

		if (old_DP4State != DP4)
		{
			digitalWrite( SMC_SW_PIN, HIGH);  		//"Taste loslassen"
			mState = ST_MAIN_SCREEN_CNT;
			ChangeDir_Button = false;
			displayMainScreen(false);
		}
		else
			if (DIR_Timer == 0)						//Timeout als Backup, damit SMC nicht blockiert falls die Umschaltung nicht klappt
			{
				digitalWrite( SMC_SW_PIN, HIGH); 	//"Taste loslassen"
				ChangeDir_Button = false;

				mState = ST_MAIN_SCREEN_CNT;
				displayMainScreen(false);
			}
		break;

    case ST_CHANGE_DIR:
    	ChangeDir_Button = true;
    	DirectionLED.blink(200,200);
		old_DP4State = DP4;
		digitalWrite( SMC_SW_PIN, LOW);		// "Taste drücken"
		DIR_Timer = 1200;					// Wartezeit setzen
		mState = ST_WAIT_CHANGE_DIR;

 	break;

	// Main screen state displays the main screen without responding to events. This is
	// effectively the home location for an idle loop that cycles through this and the
	// next state where it looks for events. Any state can return to this state to
	// enable an idle loop.
	case ST_MAIN_SCREEN:


		mState = ST_MAIN_SCREEN_CNT;
		sysMenu = false;
		selectedMenu = 0;
		displayMainScreen(false);
		break;

	// Main screen state that responds to events. This state is an entry point for
	// the menu structure and allows setting and display of operational variables.


	case ST_MAIN_SCREEN_CNT:
		// A button held event will enter the System Menu
		if (mEvent == EV_BTNHD)
		{
			mState = ST_MENU_SCREEN;
			selectedMenu = 0;
			mEvent = EV_NONE;
			displayMenuType1( FPSTR(LS_SYSMENU), FPSTR( LS_GEARENC), FPSTR( LS_TEMPERATUR ), FPSTR( LS_EXIT ), 0 );
		}
		else

			{
			if (Security_Switch_Closed)
			{
			SpindleRotational_speed = (uint16_t) GetCalcedRPM();

				// Rotary encoder events will change the Spindel RPM.
				if (mEvent == EV_ENCUP || mEvent == EV_ENCDN)
				{
					if (mEvent == EV_ENCUP) MotorRotational_speed =
							MotorRotational_speed < MAX_ROTATIONALSPEED ? MotorRotational_speed + encDelta : MAX_ROTATIONALSPEED;
					else
						MotorRotational_speed = MotorRotational_speed > MIN_ROTATIONALSPEED	 ? MotorRotational_speed - encDelta : MIN_ROTATIONALSPEED	;


					MotorRotational_speed = MotorRotational_speed < MIN_ROTATIONALSPEED	 ? MIN_ROTATIONALSPEED	 :
										MotorRotational_speed > MAX_ROTATIONALSPEED ? MAX_ROTATIONALSPEED : MotorRotational_speed;


					SpindleRotational_speed = (uint16_t) GetCalcedRPM();

					mEvent = EV_NONE;

					if (Runing)
						{
						 SetDrehzahl(MotorRotational_speed);
						 pData.Last_RPM = MotorRotational_speed;
						}

				}
			}

				displayMainScreen(false);
			}

		break;

	// The first menu in the menu structure. This is accessed from the main screen
	// by a button press event.
	case ST_MENU_SCREEN:
		sysMenu = true;
		StartLED.Off();
		// A button press event will enter the next level of the menu structure. There are
		// three items in the menu to decide which new menu is entered.
		if ( mEvent == EV_BTNCL ) {
			mEvent = EV_NONE;
			selectedMainMenu = selectedMenu;

			// Enter a sub-menu to select more options.
			if ( selectedMainMenu == 0 )
			{

				mState = ST_GEARENC_MENU;
				selectedMenu = 0;

				displayMenuType1(FPSTR(LS_DACMENU), FPSTR(LS_GEAR), FPSTR(LS_ENCSLOTS), FPSTR(LS_EXIT), 0);

			}
			// Allow settingge.
			else if (  selectedMainMenu == 1 )
			{
				mState = ST_TEMP_MENU;
				selectedMenu = 0;
				displayMenuType1(FPSTR(LS_TEMPALM), FPSTR(LS_HIGHT), pData.TCelsius ? FPSTR(  LS_CEL ) : FPSTR( LS_FAH ), FPSTR(LS_EXIT),0);
			}
			// Exit
			else if ( selectedMainMenu == 2 )
				{
				mState = ST_MAIN_SCREEN;
				StartLED.On();
				selectedMenu = 0;
				sysMenu = false;
				}

			// Rotary encoder events will allow scrolling through the menu options.
		} else if ( mEvent == EV_ENCUP || mEvent == EV_ENCDN ) {
			if ( mEvent == EV_ENCDN ) selectedMenu = selectedMenu == 0 ? 2 : selectedMenu - 1;
			else selectedMenu = selectedMenu == 2 ? 0 : selectedMenu + 1;
			mEvent = EV_NONE;
			displayMenuType1( FPSTR(LS_SYSMENU), FPSTR( LS_GEARENC), FPSTR( LS_TEMPERATUR ), FPSTR( LS_EXIT ), selectedMenu );
		}


		break;




	case ST_GEARENC_MENU:

			// A button press event will enter the next level of the menu structure. There are
			// three items in the menu to decide which new menu is entered.
			if (mEvent == EV_BTNCL)
			{
				mEvent = EV_NONE;

				selectedSubMenu = selectedMenu;
				// DAC Settings base Volt value
				if (selectedSubMenu == 0)
				{
					displayMenuType1(FPSTR(LS_GEARMENU), FPSTR(LS_DRIVERATIO), FPSTR(LS_HIRATIO), FPSTR(LS_LORATIO), 0);
					selectedMenu = 0;
					mState = ST_GEAR_MENU;
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

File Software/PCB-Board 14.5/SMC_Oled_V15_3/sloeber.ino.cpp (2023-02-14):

#ifdef __IN_ECLIPSE__
//This is a automatic generated file
//Please do not modify this file
//If you touch this file your change will be overwritten during the next build
//This file has been generated on 2023-01-20 08:47:57

#include "Arduino.h"
#define _SMC_OLED_V14_
#include <Arduino.h>
#include <SPI.h>
#include <Wire.h>
#include <avr/wdt.h>
#include <gfxfont.h>
#include <Adafruit_SSD1306.h>
#include <EEPROM.h>
#include <OneWire.h>
#include <DallasTemperature.h>
#include "ClickEncoder.h"
#include "MCP4725.h"
#include "TimedBlink.h"
#include "SMC_Oled_V15.h"

void wdt_init(void) ;
void reset_mcusr( void ) ;
ISR(TIMER2_COMPA_vect) ;
void init_Timer2() ;
uint8_t DebouncePin(uint8_t pin)  	 									 ;
void setupTimer1() ;
ISR(TIMER1_OVF_vect,ISR_NOBLOCK)			 ;
ISR(TIMER1_CAPT_vect)						 ;
uint16_t GetCalcedRPM()  ;
void setup() ;
void loop() ;
void stateMachine() ;
void checkTemperatur() ;
void checkForBtnEvent() ;
void checkEncoderEvent() ;
void checkForDP4Event() ;
void displayMenuType0( const __FlashStringHelper *title,                        const __FlashStringHelper *line1,                        const __FlashStringHelper *line2,                        uint8_t SelectedItem ) ;
void displayMenuType1( const __FlashStringHelper *title,                        const __FlashStringHelper *line1,                        const __FlashStringHelper *line2,                        const __FlashStringHelper *line3,                        uint8_t SelectedItem ) ;
void displayMenuType2( const __FlashStringHelper *title,                        const char *value,                        const __FlashStringHelper *units ) ;
void setTextProp( uint8_t size, uint8_t xpos, uint8_t ypos, uint16_t color, boolean invert ) ;
void drawStatusLine() ;
void displayMainScreen(bool signaled) ;
void SetDAC_Volt (uint16_t Volt) ;
int16_t SetDrehzahl(int16_t Drehzahl) ;
void displayHighTemperature() ;
void displaySecurityStop() ;
void displayEEPROM_Reset();
void message( const __FlashStringHelper *line1,               const __FlashStringHelper *line2,               const __FlashStringHelper *line3,               uint8_t displayTime ) ;
void splash() ;
char *valStr( char *str, uint16_t val_u, vf_Type fType ) ;
void resetEeprom( boolean full ) ;
bool loadEeprom() ;
void updateEeprom(bool force) ;
uint8_t get_key_press( uint8_t key_mask ) ;
uint8_t get_key_release(uint8_t key_mask) ;
uint8_t get_key_state(uint8_t key_mask)  ;
int getFreeRAM() ;


#include "SMC_Oled_V15.ino"

#endif

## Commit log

2022-05-05 Update Schematic
2022-05-06 Update Board , Schematic
2022-05-11 diverse Änderungen
    [Frontplatte_V1.dxf, ~Frontplatte_V1.dxf]
2022-05-31 Diverse Fehler beseitigt, siehe Readme
    [SMC_FrontPanel_ExtensionBoard_Step2_V12_1.brd, SMC_FrontPanel_ExtensionBoard_Step2_V12_1.sch]
2022-06-03 Fehlerbeseitigung siehe Readme
    [SMC_FrontPanel_ExtensionBoard_Step2_V12_2.brd, SMC_FrontPanel_ExtensionBoard_Step2_V12_2.sch]
2022-06-05 Delete SMC_FrontPanel_ExtensionBoard_Step2_V12_2.brd
    Gravierender Fehler im Layout
    [SMC_FrontPanel_ExtensionBoard_Step2_V12_2.brd]
2022-06-05 Delete SMC_FrontPanel_ExtensionBoard_Step2_V12_2.sch
    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
    [SMC_FrontPanel_ExtensionBoard_Step2_V12_2.sch]
2022-06-21 Diverse Änderungen an der Platine
2022-06-22 Update Revision 14.2 J3 Ausrichtung getauscht um fertige Kabel verwenden zu können. Kosmetik
    [SMC_FrontPanel_ExtensionBoard_Step2_V14_2.brd, SMC_FrontPanel_ExtensionBoard_Step2_V14_2.sch]
2022-06-22 remove old version
    [SMC_FrontPanel_ExtensionBoard_Step2_V14_1.sch]
2022-07-07 Änderungen an der Platine
    [SMC_FrontPanel_ExtensionBoard_Step2_V14_2.brd, SMC_FrontPanel_ExtensionBoard_Step2_V14_2.sch]
2022-07-26 Bilder vom Motoreinbau in EDM300
2022-09-05 geplante Änderungen
    [Frontplatte_V4.dxf, Frontplatte_V5.dxf]
2022-11-09 diverse updates, pictures etc.
    [Drehzahlsensor_Halterung.dxf, MagnetEncoderRad.dxf]
2022-11-11 Directory and new Hardwareversion
    [SMC_FrontPanel_ExtensionBoard_V14_5.brd, SMC_FrontPanel_ExtensionBoard_V14_5.sch, SMC_FrontPanel_ExtensionBoard_V14_5_BOM.ods]
2022-11-11 New ISO-Interface
    [SMC_ISO_Interface_V2_0.brd, SMC_ISO_Interface_V2_0.sch]
2022-11-15 updates und Test
    [SMC_FrontPanel_ExtensionBoard_V14_5.brd, SMC_FrontPanel_ExtensionBoard_V14_5.sch]
2022-11-16 wrong files corrected
    [SMC_FrontPanel_ExtensionBoard_V14_5.brd, SMC_FrontPanel_ExtensionBoard_V14_5.sch]
2022-12-01 !!Servere Error in the footprint of the Arduino Micro!!, do not connect the left connector (with RxD,TxD,DTR, etc.) to the board.
    [SMC_FrontPanel_ExtensionBoard_V14_5.brd, SMC_FrontPanel_ExtensionBoard_V14_5.sch]
2023-02-14 PCB Board 14.5 Hard and Software
    [SMC_FrontPanel_ExtensionBoardV8_SMD.brd, SMC_FrontPanel_ExtensionBoardV8_SMD.sch]
2023-03-22 Firstview of ISO Interface 4.4 with Mach3 Option or external potentiometer for speedcontrol and switch for direction change
2023-09-26 Files waren unvollständig
    [SMC_FrontPanel_ExtensionBoard_V14_5.brd, SMC_FrontPanel_ExtensionBoard_V14_5.sch]
2023-09-26 diverse Updates und Ergänzungen
    [SMC_FrontPanel_ExtensionBoard_V14_5_BOM.ods, SMC_FrontPanel_ExtensionBoard_V14_5_BOM_V2.ods]
2023-09-26 Adding Gerberfiles
    [SMC_FrontPanel_ExtensionBoard_V14_5.GBL, SMC_FrontPanel_ExtensionBoard_V14_5.GBO, SMC_FrontPanel_ExtensionBoard_V14_5.GBP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]
2024-01-24 Do not equip R27,R28 if the encoder used has a circuit board with resistors
    [SMC_FrontPanel_ExtensionBoard_V14_5_BOM_V2.ods, SMC_FrontPanel_ExtensionBoard_V14_5_BOM_V3.ods]
2024-03-13 some minor changes
    [SMC_FrontPanel_ExtensionBoard_V14_5_BOM_V3.ods]

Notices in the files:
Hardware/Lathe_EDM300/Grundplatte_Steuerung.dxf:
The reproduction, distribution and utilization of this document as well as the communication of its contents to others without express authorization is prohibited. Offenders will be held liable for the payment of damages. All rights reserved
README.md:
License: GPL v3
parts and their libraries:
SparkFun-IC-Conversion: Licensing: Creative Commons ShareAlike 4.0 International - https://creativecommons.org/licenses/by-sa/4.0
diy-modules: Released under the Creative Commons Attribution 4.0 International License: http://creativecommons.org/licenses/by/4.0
